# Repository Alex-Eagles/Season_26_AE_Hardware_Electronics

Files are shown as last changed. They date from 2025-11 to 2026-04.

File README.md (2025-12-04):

```mermaid
graph LR
    %% --- ENHANCED STYLES ---
    classDef input fill:#ffe6e6,stroke:#cc0000,stroke-width:3px,color:#000;
    classDef hvBus fill:#ff9999,stroke:#990000,stroke-width:5px,color:#fff,font-weight:bold;
    classDef reg12 fill:#cce5ff,stroke:#0047ab,stroke-width:3px,color:#000,font-weight:bold;
    classDef reg5 fill:#ccffcc,stroke:#009900,stroke-width:3px,color:#000,font-weight:bold;
    classDef load fill:#f0f0f0,stroke:#333333,stroke-width:2px,stroke-dasharray: 5 5,color:#000;
    classDef protect fill:#fffacd,stroke:#ff8c00,stroke-width:2px,color:#000;

    %% --- INPUT STAGE ---
    subgraph INPUT_STAGE [Input & Protection]
        BAT["<b>Input Source</b><br/>XT60 Connector<br/>4S LiPo (12.0V-16.8V)"]:::input
        FUSE["<b>Fuse</b><br/>Littelfuse 0451<br/>20A Fast Blow"]:::protect
        PMOS["<b>Rev. Polarity Protection</b><br/>AO4407A (P-MOS)<br/>-30V / -12A"]:::protect
    end

    %% --- MAIN BUS ---
    BUS_HV["Protected<br/>HV Rail<br/>(12V-16.8V)"]:::hvBus

    %% --- CONNECTIONS ---
    BAT --> FUSE --> PMOS --> BUS_HV

    %% --- HIGH POWER LOADS ---
    subgraph HV_LOADS [Direct Battery Loads]
        MOOK["<b>Load: Mauch</b> <br/>High Current<br/>Imauch: ~2-3A"]:::load
        CAM["<b>Load: Camera</b><br/>Input: 12-17V<br/>Icamera: ~1-2A"]:::load
        BUS_HV -->|Pass-through| MOOK
        BUS_HV -->|Pass-through| CAM
    end

    %% --- 12V MOTOR REGULATION ---
    subgraph MOTOR_STAGE [Motor Power & EMF Control]
        BUCK12["<b>12V Buck Converter</b><br/>Part: <b>MPS MP8762</b><br/>Vin: 12-18V | Vout: 12V<br/>Icont: 10A | Ipeak: 15A"]:::reg12
        
        TVS["<b>EMF Clamp</b><br/>TVS: <b>SMCJ13A</b><br/>Breakdown: 14.4V<br/>Power: 1500W"]:::protect
        BULK["<b>Energy Absorber</b><br/>Cap: 470uF<br/>Low-ESR Electrolytic"]:::protect
        
        MOTORS["<b>Load: Motors</b><br/>High Inrush / Back-EMF"]:::load
        LDOH["<b>Positive Fixed Voltage LDO</b><br/>Part: <b>HGSEMI LM7809T</b><br/>In: 12V-18V | Out:  9V<br/>Imax: 2A (Low Noise)"]:::reg5
        Herelink["<b>Load: HereLink Controller</b><br/>Input: 7-14V<br/>Iherelink: ~1-2A"]:::load
        
        BUS_HV --> BUCK12
        BUCK12 -->|Regulated 12V| MOTORS
        BUCK12 --> LDOH
        LDOH -->  Herelink
        BUCK12 -.- TVS
        BUCK12 -.- BULK
    end

    %% --- LOGIC REGULATION ---
    subgraph LOGIC_STAGE [Digital Logic Power]
        BUCK5["<b>5V Buck Converter</b><br/>Part: <b>TI TPS563201</b><br/>Vin: 12-17V | Vout: 5V<br/>Imax: 3A"]:::reg5
        
        LDO33["<b>Load: 3.3V LDO</b><br/>Part: <b>TI TLV75733</b><br/>Vin: 5V | Vout: 3.3V<br/>Imax: 1A (Low Noise)"]:::reg5
        
        FC["<b>Load: 5V Peripherals</b><br/>(Flight Controller)"]:::load
        GPS["<b>Load: 5V Peripherals</b><br/>(GPS)"]:::load
        COMP["<b>Load: 5V Peripherals</b><br/>(NVIDIA Jetson Nano Developer Kit)"]:::load
        LIDAR["<b>Load: 5V Peripherals</b><br/>(SF45/B  Lidar Sensor)"]:::load
        TEL["<b>Load: 5V Peripherals</b><br/>(Telemetry)"]:::load
        RC["<b>Load: 5V Peripherals</b><br/>(Spektrum AR6200 Reciever support DSMX)"]:::load

        MCUST["<b>Load: 3.3V MCU</b><br/>(STM32)"]:::load
        MCUES["<b>Load: 3.3V MCU</b><br/>(ESP32)"]:::load

        BUS_HV --> BUCK5
        BUCK5 --> FC
        BUCK5 --> RC       
        BUCK5 --> GPS
        BUCK5 --> COMP
        BUCK5 --> LIDAR
        LDO33 --> MCUST
        LDO33 --> MCUES
        BUCK5 --> TEL
        BUCK5 -->|"Cascade (Eff. Improvement)"| LDO33
    end
    click BAT "https://www.hobbytown.com/gens-ace-4s-lipo-battery-60c-14.8v-7200mah-gea72004s60d/p1336145" "Gens Ace 4S LiPo Battery 60C Datasheet"
    click FUSE "https://www.lcsc.com/product-detail/C178980.html?s_z=n_0451020.MRL" "Littelfuse 0451020.MRL Datasheet"
    click PMOS "https://www.lcsc.com/product-detail/C16072.html?s_z=n_AO4407A" "AO4407A (P-MOS) Datasheet"
    click TVS "https://www.lcsc.com/product-detail/C43060567.html?s_z=n_SMCJ13A" "RUILON SMCJ13A Datasheet"
    click BULK "https://www.lcsc.com/product-detail/C127917.html?s_z=n_35PX470MEFC10X12.5" "Rubycon 35PX470MEFC10X12.5 Datasheet"
    click BUCK12 "https://www.lcsc.com/product-detail/C10002.html?s_z=n_TI%2520LM2596SX-5.0%252FNOPB" "TI LM2596SX-5.0/NOPB Datasheet"
    click BUCK5 "https://www.lcsc.com/product-detail/C116592.html?s_z=n_TI%2520TPS563201" "TI TPS563201DDCR Datasheet"
    click LDO33 "https://www.lcsc.com/product-detail/C485517.html?s_z=n_%2520TI%2520TLV75733" "TI TLV75733PDBVR Datasheet"
    click MOOK "https://mauch-electronic.com/products/016-pl-2-6s-bec-2x5-35v-with-cfk-enclosure" "Mauch Datasheet"
    click CAM "https://siyi.biz/siyi_file/A8%20mini/A8%20mini%20User%20Manual%20v1.6.pdf" "Open Siyi A8 Manual"
    click Herelink "https://docs.cubepilot.org/user-guides/herelink/herelink-overview" "Open Herelink Guide"
    click FC "https://ardupilot.org/copter/docs/common-thecubeorange-overview.html" "Open Orange Cube Overview"
    click COMP "https://components101.com/development-boards/nvidia-jetson-nano-developer-kit" "Open Jetson Nano Specs"
    click GPS "https://docs.cubepilot.org/user-guides/here-3/here-3-manual" "Open Here3+ Manual"
    click LIDAR "https://acroname.com/sites/default/files/assets/sf45_-_lidar_datasheet_-_rev_1.pdf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" "Open SF45 LiDAR Datasheet"
    click TEL "https://files.rfdesign.com.au/Files/documents/RFD900x%20DataSheet%20V1.2.pdf" "Open RFD900x Datasheet"
    click MCUST "https://www.st.com/en/microcontrollers-microprocessors/stm32-32-bit-arm-cortex-mcus.html" "Open STM32 Page"
    click MCUES "https://www.espressif.com/en/products/socs/esp32" "Open ESP32 Page"
    click RC "https://www.spektrumrc.com/product/dsm2-ar6200-6-channel-receiver-ultralite/SPMAR6200.html" "Open Spektrum AR6200 Page"
    click LDOH "https://www.lcsc.com/product-detail/C507141.html?s_z=n_LM7809" "HGSEMI LM7809T Datasheet"
```

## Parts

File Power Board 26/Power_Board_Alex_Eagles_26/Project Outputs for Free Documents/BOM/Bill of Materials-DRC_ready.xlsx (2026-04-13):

Comment | Description | Designator | Footprint | LibRef | Quantity
100nF | CAP 100nF 50V X7R ±10% 0603 Ceramic Capacitors RoHS | C1, C3 | CAP_100nF | CAP_100nF | 2
CAP_4.7uF | CAP 4.7uF 25V X7R ±10% 1206 Ceramic Capacitors RoHS | C2 | CAP_4.7uF | CAP_4.7uF | 1
10uF | CAP 10uF X7R ±10% 1206 Ceramic Capacitors RoHS | C4, C5, C7, C8, C10, C11, C13, C14, C15 | CAP_10uF | CAP_10uF | 9
22uF | CAP 22uF 25V X5R ±20% 0805 Ceramic Capacitors RoHS | C6, C9, C12, C19, C20, C21, C22, C23 | CAP_22uF | CAP_22uF | 8
100nF, 50V | CAP CER 0.1UF 50V X7R 0402 | C16, C18, C27 | CAP_0402 | CAP_0402_0.1UF | 3
0.33uF | 47nF ±10% 50V Ceramic Capacitor X7R 0603 | C17, C26 | CAP_100nF | CAP_0603_47nf | 2
Cap_0603_30pf | 30pF ±5% 50V Ceramic Capacitor NP0 0603 | C24 | CAP_100nF | Cap_0603_30pf | 1
470uF | Aluminum Electrolytic Capacitor, Polarized, Aluminum (wet), 35V, 20% +Tol, 20% -Tol, 470uF | C25 | CAP_TH_5mmP | CAP_470uF | 1
Zener Diode | Zener Diode Independent 12V 200mW Surface Mount SOD-323 | D1 | DIO_BZT52C12S_RRG | BZT52C12S | 1
Diode | 1A 17.2V 1.5kW@10/1000us 14V DO-214AB(SMC) TVS Diodes RoHS | D2 | SMCJ14A | SMCJ14A | 1
TVS-SMCJ13A | 21.5V 1.5kW@10/1000us 13V DO-214AB(SMC) TVS Diodes RoHS | D3 | SMCJ14A | SMCJ13A | 1
Fast Blow | 451 Series - NANO2®Fast-Acting Subminiature Surface Mount Fuse, 20 A, 65 VAC 65 VDC, RoHS | F1 | FP-0451-MFG | 0451020.MRL | 1
XT60-M |  | J1, J2 | XT60PW-M | XT60PW-M | 2
XT30-F |  | J3 | XT30PW-F | XT30PW-F | 1
JST_GH_V6 | BM06B-GHS-TBT | J4 | JST_GH_V6 | JST_GH_V6 | 1
SM02B-GHS-TB(LF)(SN) | CONN HEADER SMD R/A 2POS 1.25MM | J5 | FP-SM02B-GHS-TB_LF_SN-MFG | CMP-2000-07076-2 | 1
MOTOR_PWR_UNIV |  | J6 | MOTOR_PWR_UNIV_FOOTPRINT | MOTOR_PWR_UNIV | 1
22uH | 22uH Magnetic Shielded Inductor 7A SMD,12.3x12.3mm Fixed Inductors RoHS | L1 | 12.3x12.3 - duplicate | IND_12.3_22uH | 1
IND_5.6uH | 5.6uH 25mΩ 13A Molded Inductor ±20% SMD,11.5x10mm Fixed Inductors RoHS | L2 | 11.5X10 | IND_5.6uH | 1
P-MOS | 3.1W 38mΩ@5V,10A SOIC-8 Single FETs, MOSFETs RoHS | Q1 | AO4407A | AO4407A | 1
10K | RES SMD 10K OHM 1% 1/16W 0402 | R1 | RES_SMD_0402 | RES_0402_10K | 1
3.9k | Resistor, 100mW 3.9kΩ 75V ±100ppm/℃ Thick Film Resistor ±1% 0603 Chip Resistor - Surface Mount RoHS | R4 | RES_3.9K | RES_0603_3.9K | 1
30k | Resistor,50mW 30kΩ 25V ±200ppm/℃ Thick Film Resistor ±1% 0201 Chip Resistor - Surface Mount RoHS | R5 | RES_30K | RES_0201_30K | 1
100 | 100mW 100Ω 75V Thick Film Resistor ±100ppm/℃ ±1% 0603 Chip Resistor - Surface Mount RoHS | R6, R8, R10 | RES_SMD_0603 | RSE_0603_100 | 3
300 | 300Ω ±1% 100mW 0603 Thick Film Resistor | R7 | RES_SMD_0603 | RES_0603_300 | 1
32.8 | 300Ω ±1% 100mW 0603 Thick Film Resistor | R9, R11 | RES_SMD_0603 | RES_0603_300 | 2
RES 169kΩ ±0.1% 100mW 0603 | 100mW Thin Film Resistor ±0.1% ±10ppm/℃ 169kΩ 0603 Chip Resistor - Surface Mount ROHS | R12 | RES_SMD_0603 | RES_0603_169K | 1
RES 36.1kΩ ±0.1% 100mW 0603 | 100mW Thin Film Resistor ±25ppm/℃ ±0.1% 36.1kΩ 0603 Chip Resistor - Surface Mount ROHS | R13 | RES_SMD_0603 | RES_0603_36.1K | 1
RES 52.3kΩ ±1% 100mW 0603 | Res Thick Film 0603 52.3K Ohm 1% 0.1W(1/10W) ±100ppm/C Pad SMD Automotive T/R | R14 | RES_SMD_0603 | RES_0603_52.3K | 1
100K | 100mW 100kΩ 75V Thick Film Resistor ±100ppm/℃ ±1% 0603 Chip Resistor - Surface Mount RoHS | R16 | RES_SMD_0603 | RES_0603_100K | 1
RES 49.9Ω ±1% 62.5mW 0402 | SMD Chip Resistor, 49.9 Ohm, ± 1%, 63 mW, 0402 [1005 Metric], Thick Film, General Purpose | R18 | RES_SMD_0402 | RES_0402_49.9 | 1
383kΩ | 100mW 100Ω 75V Thick Film Resistor ±100ppm/℃ ±1% 0603 Chip Resistor - Surface Mount RoHS | R19 | RES_SMD_0603 | RSE_0603_100 | 1
RES 20kΩ ±1% 100mW 0603 | 100mW Thick Film Resistors 75V ±100ppm/℃ ±1% 20kΩ 0603 Chip Resistor - Surface Mount ROHS | R20 | RES_SMD_0603 | RES_0603_20K | 1
AOZ1282CI | Converter DC/DC; buck; Vout: 0.8-30V; Vin: 4.5-36V; 1.2A; 0.45MHz; -40+85 deg.C; SMD; SOT23 | U1 | AOZ1282CI | AOZ1282CI | 1
AMS1117-5.0 | 18V Positive Fixed 5V SOT-89-3 Voltage Regulators - Linear, Low Drop Out (LDO) Regulators RoHS | U2, U3, U4 | AMS1117-5.0 | AMS1117-5.0 | 3
TPS56A37RPAR | Buck Switching Regulator IC Adjustable 0.6V~13V 1 Output 10A VQFN-HR-10(3x3) | U5 | RPA0010A-MFG | TPS56A37RPAR | 1
UA7810CKTTR |  | U6 | UA7810CKTTR | UA7810CKTTR | 1

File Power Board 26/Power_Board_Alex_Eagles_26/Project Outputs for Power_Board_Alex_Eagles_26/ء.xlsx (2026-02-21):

Comment | Description | Designator | Footprint | Quantity | manufacturer part number | manufacturer | LibRef | LCSC Part Number | LCSC Part | LCSC Link | Supplier Part Number 1 | supplier part number | Suplier part number | supplier
100nF | CAP 100nF 50V X7R ±10% 0603 Ceramic Capacitors RoHS | C1, C3 | CAP_100nF | 2 | CC0603KRX7R9BB104 | YAGEO | CAP_100nF |  |  |  |  | C14663 |  | LCSC
4.7uF | CAP 4.7uF 25V X7R ±10% 1206 Ceramic Capacitors RoHS | C2 | CAP_4.7uF | 1 | 1206B475K250NT | FH | CAP_4.7uF |  |  |  |  | C132148 |  | LCSC
10uF | CAP 10uF X7R ±10% 1206 Ceramic Capacitors RoHS | C4, C5, C7, C8, C10, C11, C13, C14, C15 | CAP_10uF | 9 | CGA5L1X7R1E106K160AC | TDK | CAP_10uF |  |  |  |  | C2168260 |  | LCSC
22uF | CAP 22uF 25V X5R ±20% 0805 Ceramic Capacitors RoHS | C6, C9, C12, C19, C20, C21, C22, C23 | CAP_22uF | 8 | CL21A226MAYNNNE | Samsung Electro-Mechanics | CAP_22uF |  |  |  |  | C602037 |  | LCSC
0.1uF | CAP CER 0.1UF 50V X7R 0402 | C16, C18 | CAP_0402 | 2 | CL05B104KB54PNC | Samsung Electro-Mechanics | CAP_0402_0.1UF | C307331 |  |  |  | C307331 |  | LCSC
0.33uF | Ceramic Capacitor 0603, 47nF ±10% 50V Ceramic Capacitor X7R 0603 | C17, C26 | CAP_100nF | 2 | CL10B473KB8NNNC, [NoParam] | Samsung Electro-Mechanics | CAP_0603_47nf |  |  |  |  | C1622, [NoParam] |  | LCSC
30pf | 30pF ±5% 50V Ceramic Capacitor NP0 0603 | C24 | CAP_100nF | 1 | CC0603JRNPO9BN300 | YAGEO | Cap_0603_30pf |  |  |  |  |  | C113797 | LCSC
470uF | Aluminum Electrolytic Capacitor, Polarized, Aluminum (wet), 35V, 20% +Tol, 20% -Tol, 470uF | C25 | CAP_TH_5mmP | 1 | 35PX470MEFC10X12.5 | Rubycon | CAP_470uF |  |  |  |  | C127917 |  | LCSC
100nF, 50V | CAP CER 0.1UF 50V X7R 0402 | C27 | CAPC1005X55N | 1 | CL05B104KB54PNC | Samsung Electro-Mechanics | CAP_0402_0.1UF | C307331 |  |  |  | C307331 |  | LCSC
Zener Diode | Zener Diode Independent 12V 200mW Surface Mount SOD-323 | D1 | DIO_BZT52C12S_RRG | 1 |  |  | BZT52C12S
Diode | 1A 17.2V 1.5kW@10/1000us 14V DO-214AB(SMC) TVS Diodes RoHS | D2 | SMCJ14A | 1 |  | YFW | SMCJ14A |  | C5270642 | https://www.lcsc.com/product-detail/C5270642.html?s_z=n_SMCJ14A
TVS | 21.5V 1.5kW@10/1000us 13V DO-214AB(SMC) TVS Diodes RoHS | D3 | SMCJ14A | 1 | SMCJ13A | RUILON | SMCJ13A |  |  |  |  | C43060567 |  | LCSC
Fast Blow | 451 Series - NANO2®Fast-Acting Subminiature Surface Mount Fuse, 20 A, 65 VAC 65 VDC, RoHS | F1 | FP-0451-MFG | 1 | 0451020.MRL | Littelfuse | 0451020.MRL |  |  |  |  | F8251CT-ND |  | DigiKey
XT60-M |  | J1, J2 | XT60PW-M | 2 | XT60PW-M | Changzhou Amass Elec | XT60PW-M |  |  |  |  | C98732 |  | LCSC
XT30-F |  | J3 | XT30PW-F | 1 | XT30U-F | Changzhou Amass Elec | XT30PW-F |  |  |  |  | C99102 |  | LCSC
JST_GH_V6 | BM06B-GHS-TBT | J4 | JST_GH_V6 | 1 | 533980671 | MOLEX | JST_GH_V6 |  |  |  |  | C277393 |  | LCSC
SM02B-GHS-TB(LF)(SN) | CONN HEADER SMD R/A 2POS 1.25MM | J5 | FP-SM02B-GHS-TB_LF_SN-MFG | 1 | SM02B-GHS-TB(LF)(SN) | JST | CMP-2000-07076-2 |  |  |  |  | C189893 |  | LCSC
MOTOR_PWR_UNIV |  | J6 | MOTOR_PWR_UNIV_FOOTPRINT | 1 |  |  | MOTOR_PWR_UNIV
22uH | 22uH Magnetic Shielded Inductor 7A SMD,12.3x12.3mm Fixed Inductors RoHS | L1 | 12.3x12.3 - duplicate | 1 |  |  | IND_12.3_22uH
5.6uH | 5.6uH 25mΩ 13A Molded Inductor ±20% SMD,11.5x10mm Fixed Inductors RoHS | L2 |  | 1 | SMS1050-5R6MT | LanTu Micro | IND_5.6uH |  |  |  |  | C5127460 |  | LCSC
P-MOS | 3.1W 38mΩ@5V,10A SOIC-8 Single FETs, MOSFETs RoHS | Q1 | AO4407A | 1 |  |  | AO4407A |  | C16072 | https://www.lcsc.com/product-detail/C16072.html?s_z=n_AO4407A
100K | RES SMD 10K OHM 1% 1/16W 0402 | R1 | RESC1005X37N | 1 | AC0402FR-0710KL | Yageo | RES_0402_10K | C144807 |  |  |  | C144807 |  | LCSC
0R | RES 0 OHM JUMPER 1/16W 0402 | R2, R3, R15, R17 | RES_SMD_0402 | 4 | RC0402JR-070RL | Yageo | RES_0402_0R | C60485 |  |  |  | C60485 |  | LCSC
3.9k | Resistor, 100mW 3.9kΩ 75V ±100ppm/℃ Thick Film Resistor ±1% 0603 Chip Resistor - Surface Mount RoHS | R4 | RES_3.9K | 1 | 0603WAF3901T5E | UNI-ROYAL | RES_0603_3.9K |  |  |  |  | C23018 |  | LCSC
30k | Resistor,50mW 30kΩ 25V ±200ppm/℃ Thick Film Resistor ±1% 0201 Chip Resistor - Surface Mount RoHS | R5 | RES_30K | 1 | RC0201FR-0730KL | YAGEO | RES_0201_30K |  |  |  |  | C138153 |  | LCSC
100 | 100mW 100Ω 75V Thick Film Resistor ±100ppm/℃ ±1% 0603 Chip Resistor - Surface Mount RoHS | R6, R8, R10 | RES_SMD_0603 | 3 |  |  | RSE_0603_100
300 | 300Ω ±1% 100mW 0603 Thick Film Resistor | R7 | RES_SMD_0603 | 1 |  |  | RES_0603_300
32.8 | 300Ω ±1% 100mW 0603 Thick Film Resistor | R9, R11 | RES_SMD_0603 | 2 |  |  | RES_0603_300
169kΩ | 100mW Thin Film Resistor ±0.1% ±10ppm/℃ 169kΩ 0603 Chip Resistor - Surface Mount ROHS | R12 | RES_SMD_0603 | 1 | RT0603BRB07169KL | Yageo Group | RES_0603_169K |  |  |  |  | C860143 |  | LCSC
36.1kΩ | 100mW Thin Film Resistor ±25ppm/℃ ±0.1% 36.1kΩ 0603 Chip Resistor - Surface Mount ROHS | R13 | RES_SMD_0603 | 1 | RT0603BRD0736K1L | Yageo Group | RES_0603_36.1K |  |  |  |  | C861351 |  | LCSC
52.3kΩ | Res Thick Film 0603 52.3K Ohm 1% 0.1W(1/10W) ±100ppm/C Pad SMD Automotive T/R | R14 | RES_SMD_0603 | 1 | AC0603FR-0752K3L | Yageo Group | RES_0603_52.3K |  |  |  |  | AC0603FR-0752K3L |  | Arrow Electronics
100K | 100mW 100kΩ 75V Thick Film Resistor ±100ppm/℃ ±1% 0603 Chip Resistor - Surface Mount RoHS | R16 | RES_SMD_0603 | 1 |  |  | RES_0603_100K
49.9Ω | SMD Chip Resistor, 49.9 Ohm, ± 1%, 63 mW, 0402 [1005 Metric], Thick Film, General Purpose | R18 | RES_SMD_0402 | 1 | RC0402FR-0749R9L | Yageo Group | RES_0402_49.9 |  |  |  |  | C87044 |  | LCSC
383kΩ | Fixed Resistor, Thin Film, 0.1W, 383000ohm, 75V, 0.1% +/-Tol, 25ppm/Cel, Surface Mount, 0603 | R19 |  | 1 | RT0603BRD07383KL | 383kΩ | RES_0603_383K |  |  |  |  | 603-RT0603BRD07383KL |  | Mouser
20kΩ | 100mW Thick Film Resistors 75V ±100ppm/℃ ±1% 20kΩ 0603 Chip Resistor - Surface Mount ROHS | R20 | RES_SMD_0603 | 1 | RC0603FR-0720KL | Yageo Group | RES_0603_20K |  |  |  |  | C105575 |  | LCSC
AOZ1282CI | Converter DC/DC; buck; Vout: 0.8-30V; Vin: 4.5-36V; 1.2A; 0.45MHz; -40+85 deg.C; SMD; SOT23 | U1 | AOZ1282CI | 1 | AOZ1282CI | AOS | AOZ1282CI |  |  |  | 785-1613-1-ND | C111916 |  | LCSC
AMS1117-5.0 | 18V Positive Fixed 5V SOT-89-3 Voltage Regulators - Linear, Low Drop Out (LDO) Regulators RoHS | U2, U3, U4 | AMS1117-5.0 | 3 | AMS1117-5.0 | Slkor | AMS1117-5.0 |  |  |  |  | C880753 |  | LCSC
TPS56A37RPAR |  | U5 |  | 1 | TPS56A37RPAR | TI | TPS56A37RPAR |  |  |  |  | C22392669 |  | LCSC
UA7810CKTTR LDO |  | U6 |  | 1 | TPS56A37RPAR | TI | UA7810CKTTR LDO |  |  |  |  | C22392669 |  | LCSC

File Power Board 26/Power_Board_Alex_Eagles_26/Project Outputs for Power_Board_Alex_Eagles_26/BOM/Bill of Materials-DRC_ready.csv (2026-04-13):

Designator | LibRef | Quantity | Comment | LCSC Part Number | LCSC Part | Manufacturer Part Number | Supplier Part Number | Suplier part number | Supplier | Manufacturer
C1, C3 | CAP_100nF | 2 | 100nF |  |  | CC0603KRX7R9BB104 | C14663 |  | LCSC | YAGEO
C2 | CAP_4.7uF | 1 | CAP_4.7uF |  |  | 1206B475K250NT | C132148 |  | LCSC | FH
C4, C5, C7, C8, C10, C11, C13, C14, C15 | CAP_10uF | 9 | 10uF |  |  | CGA5L1X7R1E106K160AC | C2168260 |  | LCSC | TDK
C6, C9, C12, C19, C20, C21, C22, C23 | CAP_22uF | 8 | 22uF |  |  | CL21A226MAYNNNE | C602037 |  | LCSC | Samsung Electro-Mechanics
C16, C18, C27 | CAP_0402_0.1UF | 3 | 100nF, 50V | C307331 |  | CL05B104KB54PNC | C307331 |  | LCSC | Samsung Electro-Mechanics
C17, C26 | CAP_0603_47nf | 2 | 0.33uF |  |  | CL10B473KB8NNNC | C1622 |  | LCSC | Samsung Electro-Mechanics
C24 | Cap_0603_30pf | 1 | Cap_0603_30pf |  |  | CC0603JRNPO9BN300 |  | C113797 | LCSC | YAGEO
C25 | CAP_470uF | 1 | 470uF |  |  | 35PX470MEFC10X12.5 | C127917 |  | LCSC | Rubycon
D1 | BZT52C12S | 1 | Zener Diode
D2 | SMCJ14A | 1 | Diode |  | C5270642 |  |  |  |  | YFW
D3 | SMCJ13A | 1 | TVS-SMCJ13A |  |  | SMCJ13A | C43060567 |  | LCSC | RUILON
F1 | 0451020.MRL | 1 | Fast Blow |  |  | 0451020.MRL | C178980 |  | LCSC | Littelfuse
J1, J2 | XT60PW-M | 2 | XT60-M |  |  | XT60PW-M | C98732 |  | LCSC | Changzhou Amass Elec
J3 | XT30PW-F | 1 | XT30-F |  |  | XT30U-F | C99102 |  | LCSC | Changzhou Amass Elec
J4 | JST_GH_V6 | 1 | JST_GH_V6 |  |  | 533980671 | C277393 |  | LCSC | MOLEX
J5 | CMP-2000-07076-2 | 1 | SM02B-GHS-TB(LF)(SN)
J6 | MOTOR_PWR_UNIV | 1 | MOTOR_PWR_UNIV
L1 | IND_12.3_22uH | 1 | 22uH
L2 | IND_5.6uH | 1 | IND_5.6uH |  |  | SMS1050-5R6MT | C5127460 |  | LCSC | LanTu Micro
Q1 | AO4407A | 1 | P-MOS |  | C16072
R1 | RES_0402_10K | 1 | 10K | C144807 |  | AC0402FR-0710KL | C144807 |  | LCSC | Yageo
R4 | RES_0603_3.9K | 1 | 3.9k |  |  | 0603WAF3901T5E | C23018 |  | LCSC | UNI-ROYAL
R5 | RES_0201_30K | 1 | 30k |  |  | RC0201FR-0730KL | C138153 |  | LCSC | YAGEO
R6, R8, R10 | RSE_0603_100 | 3 | 100
R7 | RES_0603_300 | 1 | 300
R9, R11 | RES_0603_300 | 2 | 32.8
R12 | RES_0603_169K | 1 | RES 169kO ±0.1% 100mW 0603 |  |  | RT0603BRB07169KL | C860143 |  | LCSC | Yageo Group
R13 | RES_0603_36.1K | 1 | RES 36.1kO ±0.1% 100mW 0603 |  |  | RT0603BRD0736K1L | C861351 |  | LCSC | YAGEO
R14 | RES_0603_52.3K | 1 | RES 52.3kO ±1% 100mW 0603 |  |  | AC0603FR-0752K3L | C227953 |  | LCSC | YAGEO
R16 | RES_0603_100K | 1 | 100K
R18 | RES_0402_49.9 | 1 | RES 49.9O ±1% 62.5mW 0402 |  |  | RC0402FR-0749R9L | C87044 |  | LCSC | Yageo Group
R19 | RSE_0603_100 | 1 | 383kO
R20 | RES_0603_20K | 1 | RES 20kO ±1% 100mW 0603 |  |  | RC0603FR-0720KL | C105575 |  | LCSC | YAGEO
U1 | AOZ1282CI | 1 | AOZ1282CI |  |  | AOZ1282CI | C111916 |  | LCSC | AOS
U2, U3, U4 | AMS1117-5.0 | 3 | AMS1117-5.0 |  |  | AMS1117-5.0 | C880753 |  | LCSC | Slkor
U5 | TPS56A37RPAR | 1 | TPS56A37RPAR |  |  | TPS56A37RPAR |  |  | LCSC | TI
U6 | UA7810CKTTR | 1 | UA7810CKTTR |  |  | UA7810CKTTR | C131966 |  | LCSC | TI

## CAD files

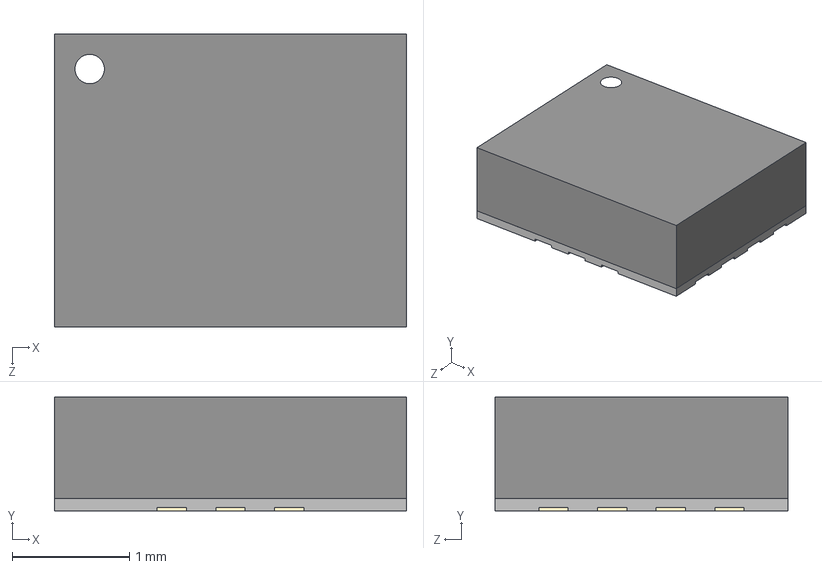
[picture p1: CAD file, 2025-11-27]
Sensors/ICM-42688-P--3DModel-STEP-1.STEP
3.00 x 0.97 x 2.50 mm

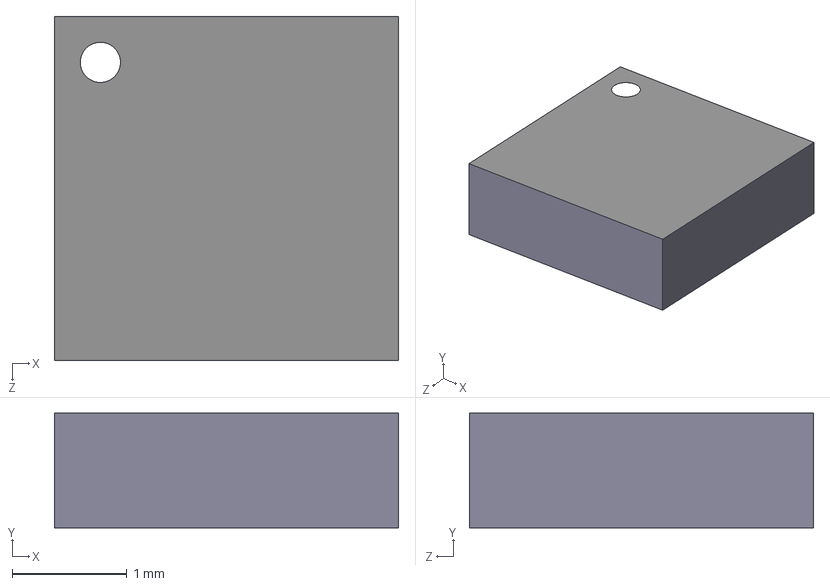
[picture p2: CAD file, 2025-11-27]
Sensors/IST8310.STEP
3.00 x 1.00 x 3.00 mm

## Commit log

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2025-11-26 added sensors folder
    [Sensors.PcbLib, Sensors.SchLib]
2025-11-27 fixed some components
    [ICM-42688-P--3DModel-STEP-1.STEP, IST8310.STEP, Sensors.PcbLib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]
2025-11-27 renamed folder
    [ICM-42688-P--3DModel-STEP-1.STEP, IST8310.STEP, Sensors.PcbLib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]
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2025-12-17 edited library structure
    [bucks_PcbLib1.PcbLib, bucks_Schlib1.SchLib]
2025-12-18 edit passive folder
    [Resistors.PcbLib, Resistors.SchLib, capacitors.PcbLib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]
2025-12-18 edited folder structure
    [Resistors.PcbLib, Resistors.SchLib, capacitors.PcbLib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]
2025-12-18 Added common footprints
    [capacitors.PcbLib, capacitors.SchLib]
2025-12-18 Add Diodes MOSFETs ICs Fuse
    [Diodes_PCB.PcbLib, Diodes_Sch.SchLib, Fuse_PCB.PcbLib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]
2025-12-18 Add RES25.5K RES154K RES93.1K
    [Resistors.PcbLib, Resistors.SchLib, capacitors.SchLib]
2025-12-18 edited resistor
    [Resistors.SchLib]
2025-12-18 edited capcitor symbols
    [Resistors.SchLib, capacitors.SchLib]
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2025-12-19 Add pcb_project folder
    [LM73100RPWR.STEP, PcbLib1.PcbLib, RUX0012A.stp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]
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2025-12-20 moved components
    removed pcb_project folder and added components to ICs folder
    [ICs_PCB.PcbLib, ICs_Sch.SchLib, LM73100RPWR.STEP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]
2025-12-20 edited some sensors and capacitors
    [Resistors.PcbLib, Sensors.PcbLib, capacitors.PcbLib]
2025-12-22 edited some components
    [Diodes_PCB.PcbLib, Diodes_Sch.SchLib, Fuse_PCB.PcbLib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]
2025-12-22 added flash memory
    [ICs_PCB.PcbLib, ICs_Sch.SchLib]
2025-12-22 added inductor folder
    [ICs_PCB.PcbLib, inductors.PcbLib, inductors.SchLib]
2025-12-22 edited inductor
    [inductors.SchLib]
2025-12-22 Added connecters folder
    [connectors.PcbLib, connectors.SchLib]
2025-12-22 USB_C with all it's components
    [Diodes_PCB.PcbLib, Diodes_Sch.SchLib, ICs_PCB.PcbLib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]
2025-12-22 REST OF USB_C COMPONENT
    [ICs_PCB.PcbLib, ICs_Sch.SchLib, connectors.PcbLib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]
2025-12-22 USB_C COMPONENT
    [inductors.PcbLib, inductors.SchLib]
2025-12-22 edit mosfets
    [MOSFETs_Sch.SchLib]
2025-12-22 added diode
    [Diodes_PCB.PcbLib, Diodes_Sch.SchLib, MOSFETs_Sch.SchLib]
2025-12-22 edited diode
    [Diodes_PCB.PcbLib, Diodes_Sch.SchLib]
2025-12-22 renamed resistors
    [Resistors.SchLib]
2025-12-22 Added Micro SD card holder
    [connectors.PcbLib, connectors.SchLib]
2025-12-22 edited resistor symbols
    symbol pins were off grid, created a new symbol and used it for all resistors
    [Resistors.SchLib]
2025-12-22 added a component
    [Diodes_PCB.PcbLib, Diodes_Sch.SchLib, Resistors.SchLib]
2025-12-22 updated fuse
    [Fuse_Sch.SchLib]
2025-12-22 edited servo rail
    [connectors.PcbLib, connectors.SchLib]
2025-12-22 added resistor
    [Resistors.SchLib]
2025-12-23 off grid pins
    [Resistors.SchLib, bucks_Schlib1.SchLib]
2025-12-24 Added 3 LDOs: 5V, 3.3V, 1.8V
    [PcbLib1.PcbLib, Schlib1.SchLib]
2025-12-25 edited stm chip symbol
    [ICs_Sch.SchLib]
2026-01-24 fixed stm symbol
    [ICs_Sch.SchLib]
2026-01-24 connection
    Did a basic connection
    [Diodes_PCB.PcbLib, Diodes_Sch.SchLib, connectors.SchLib]
2026-01-24 RAIL
    Added rail parts
    [Rail.PcbLib, Rail.SchLib]
2026-01-24 resistors layout
    [Resistors.PcbLib, Resistors.SchLib, capacitors.SchLib]
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2026-01-24 XT-connectors
    added XT connectors, 30&60, M&F
    [connectors.PcbLib, connectors.SchLib]
2026-01-25 Remove old resistor library
    [Resistors.PcbLib, Resistors.SchLib]
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2026-01-26 fixed JST connectors
    [connectors.SchLib]
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2026-01-30 Added mounting holes in connectors
    [connectors.PcbLib, connectors.SchLib]
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2026-01-30 added button 3d body
    [connectors.PcbLib]
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2026-01-30 general fixes for designators and missing footprints
    [Diodes_Sch.SchLib, Resistors.SchLib, Schlib1.SchLib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]
2026-01-31 fixed crystal 3D body
    [capacitors.PcbLib]
2026-01-31 WIP: saving work before pull
    [Digital_Logic_Power.SchDoc, MOSFETs_PCB.PcbLib, MOSFETs_Sch.SchLib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]
2026-01-31 Resolved conflicts by keeping local changes
    [connectors.SchLib]
2026-02-02 aded LDO in Powerboard sheet+added capacitor
    [Motor_Power_and_EMF_Control.SchDoc, PcbLib1.PcbLib, Schlib1.SchLib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]
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2026-02-21 edited some components,restored MOSFETs folder, and updated power board pcb
    [Alex_Eagles_Power_Board_PCB.PcbDoc, Digital_Logic_Power.SchDoc, Direct_Battery_Loads.SchDoc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]
2026-02-21 edited in buck lib
    [bucks_Schlib1.SchLib]
2026-02-22 finalized project preparing for placement
    [Alex_Eagles_Power_Board_PCB.PcbDoc, Digital_Logic_Power.SchDoc, Input_and_Protection.SchDoc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]
2026-02-22 Upload Power Board PCB
    [Alex_Eagles_Power_Board_PCB.PcbDoc, Direct_Battery_Loads.SchDoc, Input_and_Protection.SchDoc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]
2026-02-22 edited D1 footprint (zener diode)
    [Diodes_PCB.PcbLib, Diodes_Sch.SchLib]
2026-02-22 edited zener diode footprint
    [Diodes_PCB.PcbLib]
2026-02-23 edited c19,L2 footprints for power board
    [Diodes_PCB.PcbLib, Resistors.SchLib, capacitors.PcbLib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]
2026-02-23 edited U4 footprint for powerboard
    [bucks_PcbLib1.PcbLib, bucks_Schlib1.SchLib, capacitors.SchLib]
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2026-02-23 fixed some off grid symbols in sheet
    [Alex_Eagles_Power_Board_PCB.PcbDoc, Digital_Logic_Power.SchDoc, Direct_Battery_Loads.SchDoc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]
2026-02-23 edited in the sch
    [Input_and_Protection.SchDoc]
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2026-04-09 finished polygons/added test pads/deleted unions/connected flight controller pins
    [Alex_Eagles_Power_Board_PCB.PcbDoc]
2026-04-09 added gnd layer polygon
    [Alex_Eagles_Power_Board_PCB.PcbDoc]
2026-04-09 reverted some changes
    [Alex_Eagles_Power_Board_PCB.PcbDoc, Power_Board_Alex_Eagles_26.PrjPcb]
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2026-04-13 added mounting holes with their silkscreen layer
    [DRC_ready.PcbDoc]
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2026-05-25 fixed resistor library
    [Altium footprints, SMD Resistors, 2013-06-08-1.PcbLib, Resistors.PcbLib]
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2026-05-27 fixed resisor footprints
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2026-05-30 validated additiions (some resistors missing)
    [Diodes_PCB.PcbLib, Diodes_Sch.SchLib, Resistors.SchLib]
2026-05-30 fixed issues with diodes library (recompile)
    [Diodes_PCB.PcbLib, Diodes_Sch.SchLib]
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2026-06-10 layed out 10v block (by ekbal)
    [Diodes_PCB.PcbLib, Diodes_Sch.SchLib]
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
